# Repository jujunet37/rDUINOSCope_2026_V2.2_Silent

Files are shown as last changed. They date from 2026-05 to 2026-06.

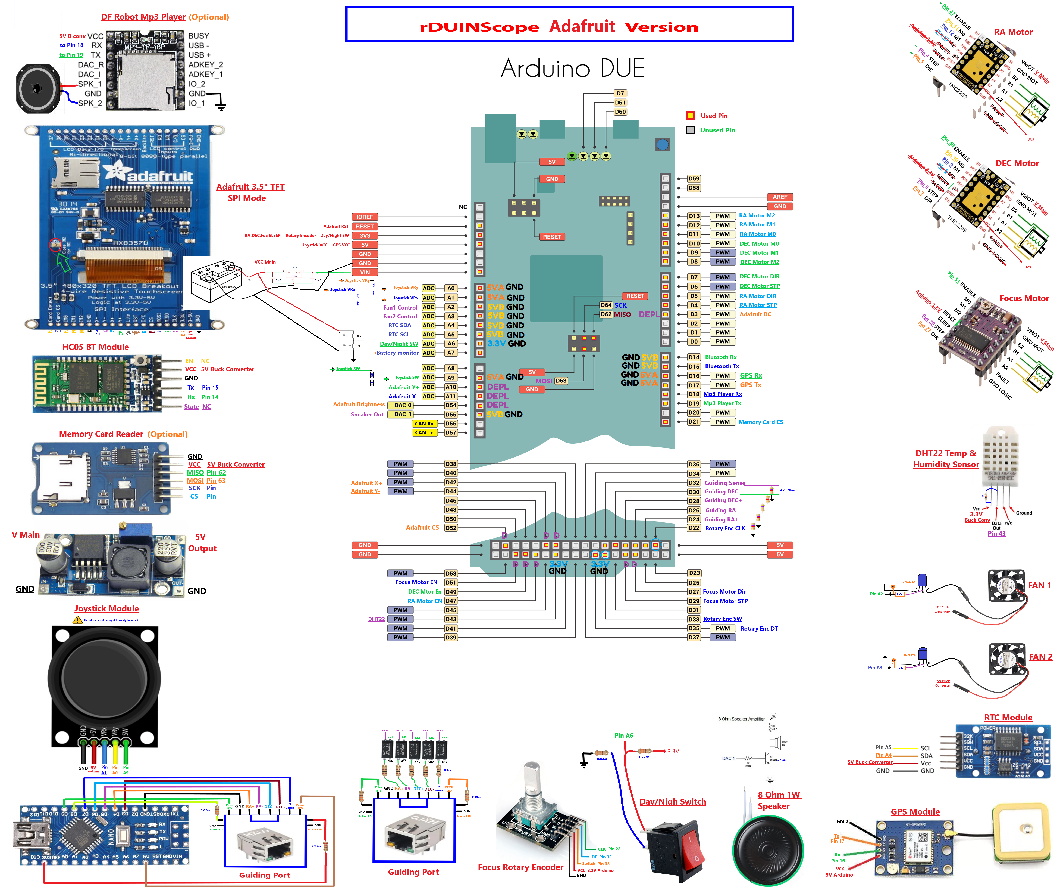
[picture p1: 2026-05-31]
Adafruit HW V.1 Wiring Diagram2.png

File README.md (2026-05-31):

# Update 24/05/2026 : rDUINOScope\_2026\_V2.2\_Silent

# 

## This is a modified version of the 10 April 2020 version of the rDUINOScope by Khairey Nouhe that works with Adafruit 3.5" 320X480 TFT SPI mode.

### New features :

* This new version need a hardware modification. It uses TMC2209 instead of DRV8825, which make the motors much more quiter.
* Joystick re-leveling, addition of very low speed manual mode.
* Modification of periodRA and DEC Timers to adjust motor speeds for these new drivers.
* Reversing motor polarity for rotation in the correct direction for these new drivers.
* Microstepping sequence moved from 1-2-4-8-16 to 8-4-16-32 for compatibility with these new drivers.
* Review of deceleration mode
* Bug fix : displayed the chain of the previous pointed-to object when loaded an object from bright star catalog : corrected.
* Speed adjusted because of lower precision on these drivers. Now 90% of "2.0 Big Update" version and 70% of "2.1 ASCOM" version, still 180% of the initial version without full step speed.

#### 

# HARDWARE REQUIREMENT :

Wire as shown in the diagram.

- Let the unused pins unplugged, and put a wire to supply the 3.3V pin from the Arduino source.
- Set the drivers to 1.5V.
To set the drivers : Measure the voltage between VREF and GND with no motors plugged, and adjust voltage with the screw.

YouTube video link : https://www.youtube.com/watch?v=LmjZzCkUyhM

---

# 

# Update 28/03/2026 : rDUINOScope\_2026\_V2.1\_ASCOM

## V2.1 major improvements : ASCOM Driver, code optimization and new search engine.

# 

### Total code revision :

* All String removed, migration to char to avoid unpredictable memory issues.
* New motor moving logic for slew, with included Arduino Due hardware timer to improve CPU performance and avoid ASCOM reading conflict.
* Speed also increase by 30% (was already doubled with previous version), so it is now 2.5x times faster to slew comparing to original version. Motors spin with less vibrations.

### New features :

* New loading menu with brand new search engine.

Be specific when searching. Engine look in the first catalog, stop when found 50 objects with the entered string. Go to the second, etc... Stop when 250 objects limit is reached. Engine don't look at planets names.

* Complete server ASCOM driver, for multiple connections with several app at the same time (Cartes du Ciel, PHD2, N.I.N.A)
* Joystick acceleration for smoothness

#### Driver support :

* GOTO object
* GOTO HOME position
* GOTO Park Position
* Set Park feature
* Set Tracking feature
* Set Rates feature
* Pier Side position
* Synchronisation
* RA/DEC reading coordinates
* ALT/AZ coordinated (calculated by the driver)
* Import GPS coordinates (LAT, LONG, ALT)
* Manual move with invert axis
* Abort move
* Autoguiding (pulse guiding) No more need an external device.

### BUG fix :

* Several stars names corrected in alignment list.
* RA/DEC coordinates : A rounding bug in coordinates made a 1m or 1' jump.
* Files on SD card may be corrupted after going into options menu (was caused by a String value)
* Meridian flip didn't occur when goto back on east and pass it a second time.
* Brightness setting woundn't work.
* BT manual move amount corrected, adaptative amount depending on DEC value
* BT slew froze the APP.
* BT slew wouldn't show telescope position during a Slew
* Display bug on OBSERVING / TRACKING line

### Known issues :

* Motors start to move when shutdown the PC with tracking ON (even with driver disconnected). Set tracking OFF before shut down the PC.

### REQUIRE :

* Arduino IDE 1.8.19

* Windows settings : Must change decimal character to "." in region settings

### Installation :

* Edit rDUIUNOScope\_FINAL and type you location on lines 191 to 193. Change worm settings (205 to 207). Flash Arduino code
* Copy files to the micro SD card (new ASCOM image files)
* Install the ASCOM driver (require ASCOM platform, tested on 7.1 Update 1

### Libraries :

* Copy to : C:\\Users\\USERNAME\\Documents\\Arduino\\libraries

* marekburiak-ILI9341\_due-13edbd2
* DHT\_sensor\_library
* TinyGPSPlus
* Touch-Screen-Library-master
* SdFat-master
* DueTimer-master
* DS3231
* Time-master
* Adafruit\_Unified\_Sensor

* Install in library manager :

* Arduino SAM Boards (32-bits ARM Cortex-M3) (v 1.6.12)

### 

### Miscellaneous :

* Setup video on YouTube.
* French : https://youtu.be/6-61nRDWkmA
* English : https://youtu.be/PrEs-5IPebA

# Update 16/07/2024 : rDUINOScope\_2024\_Big\_Update V2.0

### Corrected bugs and many new features and catalogs :

### corrected bugs :

* Previously corrected autoguiding : now works.
* Status bar : Auto and OFF superposition message for meridian flip : corrected.
* Coordinates Page : RA, DEC and HA inversion, DEC format error (missing a ":", and was in HA box : Workaround found because correct it directly make bluetooth no longer works. Now DEC in right format and BT works)
* LST and AZ/H error due to bad summer time parameters for France. Corrected for France, check the code to adjust for other countries. (same change days as for Italy (by default), but GMT + 1 for winter and GMT + 2 for summer).
* Corrected an error in dayno formula that causes a shift in RA for planets.
* Corrected an error in planets computing formulas and add precise information data.
* Corrected errors in Moon computing formulas
* RA went false or negative on Moon Goto : Corrected

### Added :

### Hardware :

* Same wiring than Khairey Nouhe design with all functionalities but focuser and fan connectors.
* Now PCB is provided, gerber files are in the package.
* Internal cooling fan, controlled by the UI.

### Software :

* Previously add dew point information.
* Previously double goto speed.
* Previously center joystick tracks and orthogonality of both axes in software (for my component, look at the previous video, 1h05m)
* Joystick directions more intuitive : left : RA return, right : RA forward.
* Add fine manual move for BlueTooth app, works great with Skysafari, works with stellarium plus but very long latency.
* Bluetooth works, tested with Skysafari 6, 7, stellarium mobile plus and Stellarium desktop.
* Add Store position utility : To memorize any position and goto back function to recall this position. Useful for keeping a frame camera when needed to go elsewhere (ex goto bright star for Bahtinov focusing and then go back to the target)
* Touchscreen calibration tool added (button was in option page but not activated). New calibration tool was created to help unshift touchzones with display. The tool can display the new correction parameters, and store it in SD card. Parameters can be fine tuned by editing "OPTION.TXT" in SD card. Four last values are : Slope in x, Slope in y, Intercept in x and intercept in y. A function can restore to default and erase SD card calibration data in case of bad calibration. Look at code comment for further informations.
* New load menu with cool JWST's creation pillars background :-)
* Checked Messier Catalog and update informations abouts objects, such as name and distance.
* Move M111 and M112, which don't exist in Messier catalog, now in NGC catalog.
* Now around 3000 objets in database !
* New NGC catalog with 2400 objects :

  * All objects in Northern hemishere down to -35° DEC, Magnitude < 13. Then filtering objects by a selection by taking into account the atmospheric extinction : ojects with Magnitude < 10 at -35° to -25° DEC, Magnitude < 11 at -25 to -20° DEC. Magnitude < 12.5 at -20 to -15° DEC. Magnitude 13 and lower for DEC > -15°.
  * NGC catalog divided in 5 parts with 480 item each. Each part with a magnitude range, for a variety of apertures.
* 186 IC catalog objetcs with same magnitude references as NGC catalog above, with no cross references with NGC.
* 172 Bright stars catalog for focusing purpose.
* 160 Double stars catalog
* 138 Variable stars catalog
* Custom catalog with up to 240 entries : completed with Collinder catalog and special objects : 84 entries.
* Deleted double references in NGC, IC catalogs and cross references with other catalogs. Priority : Messier, NGC, IC.
* All new catalogs sorted by constellation : less time to move from one to the other ! Buttons now show name, constellation and magnitude.
* Bunch of new information data (distance, separation and color for double stars, period, type and magnitudes for variable stars, etc...)
* All catalogs loaded in the same array : Same SRAM usage but now more than 3000 objects !
* New Autoguiding background : deleted circle RA, DEC, Focus. New landscape.
* Add new planet info from J2000 (1st January 2000 @ 12h GMT), previous information was approximate computed info for 2013 from J2000 data. Now starting computing from J2000 original information with better precision : On a test date, error values for internal planets was RA/DEC 4-5m/20-30'. External planets was 0-3m/2-5' (except 15-20' DEC for Mars and Neptune). Now internal planets at this test date are in range RA/DEC error : 1-2m/8-13'. External planets : 0-2m/2-7'. Tested on random dates between 2024-2044, for all planets, error are within -5m to +2m RA / -13' to 13' DEC, most values <10'.

### miscellaneous :

* Complete tutorial construction on YouTube.
* French : https://www.youtube.com/watch?v=rhm9jwSgXOs
* English : https://www.youtube.com/watch?v=H-uTFNglyio

### All changes in code are tagged by // Add JG, // End add JG, // Modif JG, for easily look at the modifications.

===========================================================

# Previous Updates From Khairey Nouhe, Giacommo Mammarella, Dessislav Gouzgounov and contributors :

### Update Friday 10/4/2020 (Fayrouz Update With ILI9341):

* The new version is built on the SdFat Library.
* It uses a modified version of marekburiak-ILI9341\_due library that has been modified specially for this project.
* New Graphical User Interface has been developed,Inspired by Dessislav Gouzgounov.
* Corrected Solar System Objects bug from last update. Thanks to (Aitor Plazaola Alcerreca) From the rDUINOScope Support Group.
* Support for Stellarium Mobile Plus has been added.
* Supports the rDUINOScope Companion Android App (will be launched soon on Google Play)!

### Hardware Changes:

* Support for PHD2 Autoguiding has been added. Thanks to the project by https://github.com/kevinferrare/arduino-st4
* A third stepper motor has been added for focus control.
* An Optional DFRobot Mp3 Player has been added for future upgrade.
* Consider the new Wiring Diagram for Hardware Changes!
===========================================================

### Update Saturday 4/5/2019 (Fayrouz Update With Solar System!):

* Removed Nextion Commands to avoid errors in compile.

### Update Tuesday 16/3/2019 (Fayrouz Update With Solar System!):

### Use IDE 1.8.5 to avoid compile errors.

Includes Giacomo Mammarellas's updated features!

* No hardware changes.
* Memory card contents are changed.
* Added Solar System objects tracking to Load Screen.
* Added Battery Power indicator to main screen, currently showing USB only, just for future upgrade.
* Added images for Solar and stellar objects to show on Main Screen. ( Memory Car items changed).
===========================================================

### Update Tuesday 3/7/2018 (Fayrouz Update!):

* Includes Giacomo Mammarellas's updated features!
* No hardware changes.
* Memory card contents are changed.
* Changed supporters logos at startup page.
* Full Hardware check and confirmation at initilize.
* More Accurate Joystick calibration at startup.
* Options' data are saved to a text file on the memory card, and will be restored and initilized during next boot.
* A new screen brightness control triangle has been added.
* New on screen messages has been added.
* Prevent (Load), (Home), (Bluetooth), and (Track) buttons to function while steppers are off. Avoiding Wrong Telescope Position coordinates while steppers are off.
* Corrected Steppers' speed during " Slew to" process . very slow>slow>fast>faster>>>>>>>>>>>fast>slow>very slow>stop>track.
* Faster browsing for Messier and treasures catalogs.
* Automatic date and time set on clockScreen() derived from GPS data: the software is able to calculate the location's time zone and to auto update from summer or winter time.
* Added an new button in Options screen to update date and time from GPS data.
* New debug mode. can be used to debug touchscreen actions.
===========================================================

### Update Saturday 23/9/2017:

### Added Giacomo Mammarellas's new features Like:

* Joypad calibration at startup. No more panic to find right values for the joypad.
* Empirial March sound function moved to confirm good initialization of the device. If no sound then you're having problems! :'(
* Automatic data and time set on clockScreen() derived from GPS data: the software is able to calculate the location's time zone and to auto update to summer or winter time.
* Custom line of text can be appended to any .csv file to display custom "Description" strings. Example: I added "rich cluster with more than 100 stars" to M11 in messier.csv
* Orange color for Name and Description when tracking objects.
* Added custom.csv wich can be used to add more custom sky objects (still to be implemented) ===========================================================

Repairs:

* Re-position Summer button at Clock Screen.
* added Green and Red colors to Screen-Timeout at the status bar.
===========================================================

## rDUINOScope

* THE WORLD'S FIRST STAND ALONE ARDUINO BASED TELESCOPE CONTROL GOTO (handheld controller).
rDUINOScope is an Open Source, Arduino Due based Telescope Control System (GOTO). Drafted as stand alone system, rDUINOScope does not need PC, Tablet or Cell Phone, nor Internet connection in order to operate and deliver stunning views! It does however supports Bluetooth and LX200 protocol to connect and be controlled by smart devices!
rDUINOScope uses database with THE BEST \~250 stellar objects ( Messier and Hidden Treasures Catalogues) and 200 stars, calculates their position on the sky and points the telescope. Implemented Alignment procedures allow for "Always in the eyepiece" experience when slewing to selected objects and once the object is in the eyepiece, the system keeps tracking it.
The best part of rDUINOScope is that it is an OPEN SOURCE SOFTWARE and HARDWARE! Few custom telescope makers have announced that they are adding or about to add it to their product line. In addition, few months ago a new HW shield board was born as a spin-off project to spare you the hassle of building your own rDUINOScope!
Published under GNU General Public License
Instructions on how to build hardware can be found on the project's website: http://rduinoscope.byethost24.com/ HACKADAY.IO Project: https://hackaday.io/project/21024-rduinoscope
Facebook: https://www.facebook.com/rDUINOScope/

### rDUINOScope v2.3.1 Boiana EQ

* Release date: 03 August 2017 Status: Stable Version Author: Dessislav Gouzgounov / Десислав Гузгнов /(deskog@gmail.com)
* v2.3.1 aims to bring all existing hardware platforms into one code base. Additionally this version introduces new features to the rDUINOScope like Screensaver, TFT brightness, MosFET to control power to DRV8825 and etc.
* Current release will also be used as a base to add the Alt/Az changes.

### New features added in v2.3.1:

* Brings all existing flavours of the hardware to use same code!
* Hardware Changes!!! - Plese reffer to the HACKADAY instructions!
* Screen Brightness control;
* Screen Auto OFF function with timeout;
* Implemented FET transistor to control power to the stepper motors;
* More BlueTooth commands added to prepare for a screenless version (or operation);
* It is now possible to control rDUINOScope without the TFT screen - so called "BLIND" version.
* BUG fixes:

  * GPS fixes;
  * SlewTo speed issues for low amperage;

### New features added in v2.3:

* Code Optimization for Performance (SlewTo now capable of speeds > 3 deg/sec);
* Added Celestial, Lunar and Solar tracking speeds;
* Added new Main Menu system for more functionality;
* Added control on 2 external devices (DEV 1 \& 2 - you can hook your Heater, Fan and etc);
* Added support for SkySafari 5 (smartphone software);
* Added build in Star Atlas showing current telescope position;
* Shows current Firmware version on Loading screen and on Bluetooth request using LX200 protocol;
* Bug fixes: o Wrong DEC movement for negative DEC values passed over Bluetooth; o LST revised in the format XX:XX;

### New features added in v2.1:

* Added “1 Star Alignment” Method;
* Added “Iterative Alignment” Method;
* Added 200 brightest stars to be used in alignment procedures;
* Added Bluetooth control from Stellarium (cloned LX200 communication protocols);
* Added Bluetooth connection with PC;
* Code has been refactored for easy reading/editing;
* Bug fixes: o Wrong DEC movement for negative DEC values; o Revised RA movement formula; o OnScreen messages have been fixed;
* Buttons move after press event was fixed;

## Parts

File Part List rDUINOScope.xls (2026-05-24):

Type | Name | Designator | Footprint | Quantity
Capacitor | Electrolytic capa 100u | C3,C4 | SMD CAP-D6.3×H5.5 | 2
Capacitor | Ceramic capa 0.33u | C1 | RAD-0.2 | 1
Capacitor | Ceramic capa 0.1u | C2,C5 | RAD-0.2 | 2
Resistor | 10K | R1 | R_AXIAL-0.3 | 1
Resistor | 20K | R2 | R_AXIAL-0.3 | 1
Resistor | 6.8K | R3 | R_AXIAL-0.3 | 1
Resistor | 330R | R4,R5 | R_AXIAL-0.3 | 2
Resistor | 47k | R6,R8,R10 | R_AXIAL-0.3 | 3
Resistor | 100k | R7,R9,R11 | R_AXIAL-0.3 | 3
Resistor | 220R | R12 | R_AXIAL-0.3 | 1
Resistor | 6.8R | R13 | R_AXIAL-0.3 | 1
Resistor | 330 | R14 | R_AXIAL-0.3 | 1
Resistor | 10k | R15 | R_AXIAL-0.3 | 1
Resistor | 100R | R16,R17,R18,R19,R20 | R_AXIAL-0.3 | 5
Resistor | 4.7k | R21,R22,R23,R24,R25 | R_AXIAL-0.3 | 5
Transistor | 2N3904(TO-92) | Q1 | TO-92-3_L5.1-W4.1-P1.27-L | 1
Transistor | 2N2222 | Q2 | TO-92-3_L4.9-W3.7-P1.27-L | 1
Transistor | 7809 MOSFET | 7809 | TO-220-3_L10.0-W4.5-P2.54-L | 1
Optocoupler | PC817 optocoupler | U5,U6,U7,U8,U4 | DIP-4_L4.6-W6.5-P2.54-LS7.6-BL | 5
Driver | DRV8825 | U2, U3 | DRV8825 | 2
Connector | RJ45 connector | RA and DEC | RJ45-TH_R-RJ45R10P-B000 | 2
Connector | RJ12 connector | AG | RJ11-TH_PCB-6P6C-90 | 1
Connector | Ribbon screen connector | SCREEN | CONN-TH_HC-ZH1.5-8A | 2
Connector | Header JST 1.25 x 2 | Fan, Speaker, switch | 1X02-1.25MM_JST | 3
Connector | Header JST 1.25 x 3 | DHT22 | 1X03-1.25MM_JST | 1
Connector | Header JST 1.25 x 4 | GPS Module | 1X04-1.25MM_JST | 1
Connector | Header JST 1.25 x 5 | Joystick, bridge x 2 | 1X05-1.25MM_JST | 3
Connector | Header JST XH 2.54 | POWERIN | HDR-TH_2P-P2.54-V-M | 1
Fan | 20x20x6mm 2 pin 5V |  | ACP2006 | 1
Type : | Name : | Reference |  | Quantity
Screen | TFT Adafruit 3,5" | 2050 (HX8357D) |  | 1
Board | Arduino Due |  |  | 1
Board | Arduino Nano | ATMega 328P |  | 1
BT module | BT | HC05 BT |  | 1
5V Buck | Based on LM2596 |  |  | 1
Joystick |  |  |  | 1
Switch | 8x8x8.4mm | ON/OFF lock L068-A |  | 1
Speaker | Speaker | 8 Ohm 1W |  | 1
GPS Module |  | GY-NEO6MV2 |  | 1
RTC module |  | DS3231 |  | 1
T°/H% sensor |  | DHT22 4 pins |  | 1
Drivers | Polulu, TI chip 8825 | DRV8825 |  | 3
Motors | Nema 17 | JK42HM40-1684 |  | 2
Holders | In GitHub package | https://www.thingiverse.com/thing:4853748
 |  | (add 2 bases and cover on thing:4682671)
 |  | replace 2 motors holders and connector squares
RJ45 cables | 1,5m lenght |  |  | 1
RJ45 cables | 1m lenght |  |  | 1
Pulleys | motor pulleys | GT2/6mm 16t trou 5mm |  | 2
Pulleys | Worm pulleys | GT2/6mm 48t trou 6mm |  | 2
Belt | belt | 6mm GT2-148 |  | 2
RJ12 cable | for Autoguiding | 50cm |  | 1
Screws
TCHC M6X20 (Hollow hexagonal head) |  |  |  | 1
TCHC M6X35 |  |  |  | 1
TBHC M3X8 (Cambered head hexagonal hollow) |  |  |  | 12
TBHC M3X20 |  |  |  | 4
nut M6 |  |  |  | 2
nut M3 |  |  |  | 8
nut M4 |  |  |  | 2
TBHC M4x25 |  |  |  | 2
washer M03 |  |  |  | 8
Autoguiding box | Plastic | 61x36x25mm |  | 1

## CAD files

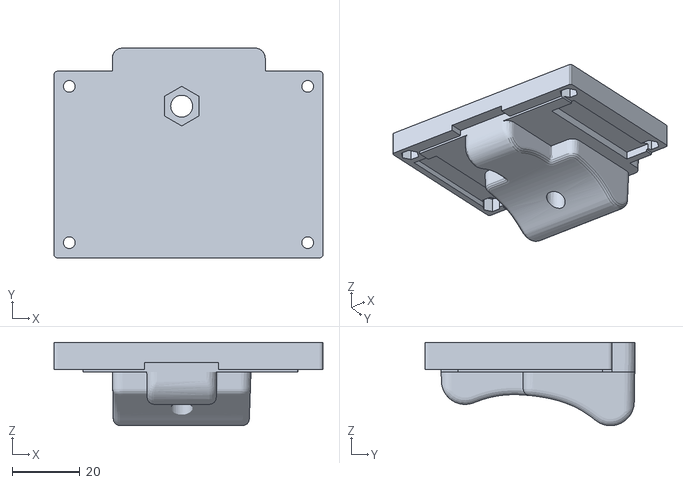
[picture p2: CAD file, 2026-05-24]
NEQ5_Holders_STL_FILES (oddvarness Thingiverse)/RA_base.stl
79.2 x 61.8 x 24.5

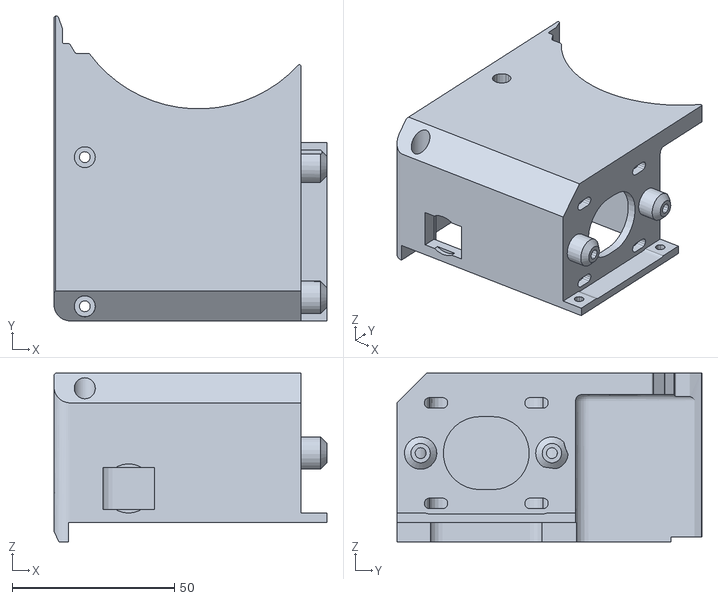
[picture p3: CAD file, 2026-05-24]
NEQ5_Holders_STL_FILES (oddvarness Thingiverse)/RA_motor_holder_V2_RJ45.STL
84.2 x 94.0 x 52.1

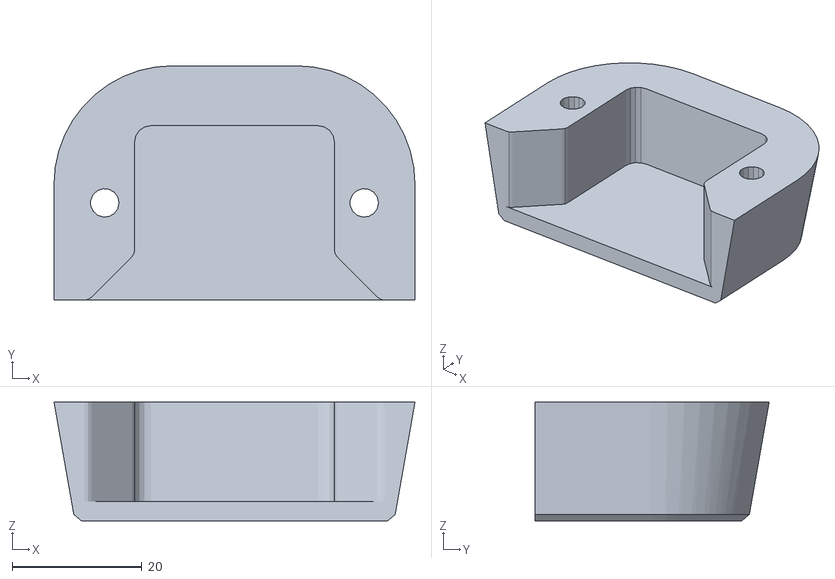
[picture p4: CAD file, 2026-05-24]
NEQ5_Holders_STL_FILES (oddvarness Thingiverse)/DEC_brace.stl
55.7 x 36.1 x 18.3

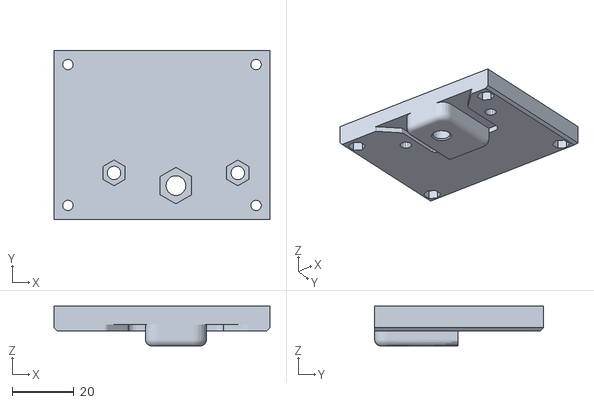
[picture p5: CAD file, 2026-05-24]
NEQ5_Holders_STL_FILES (oddvarness Thingiverse)/DEC_plate_V2.stl
69.8 x 54.5 x 12.9

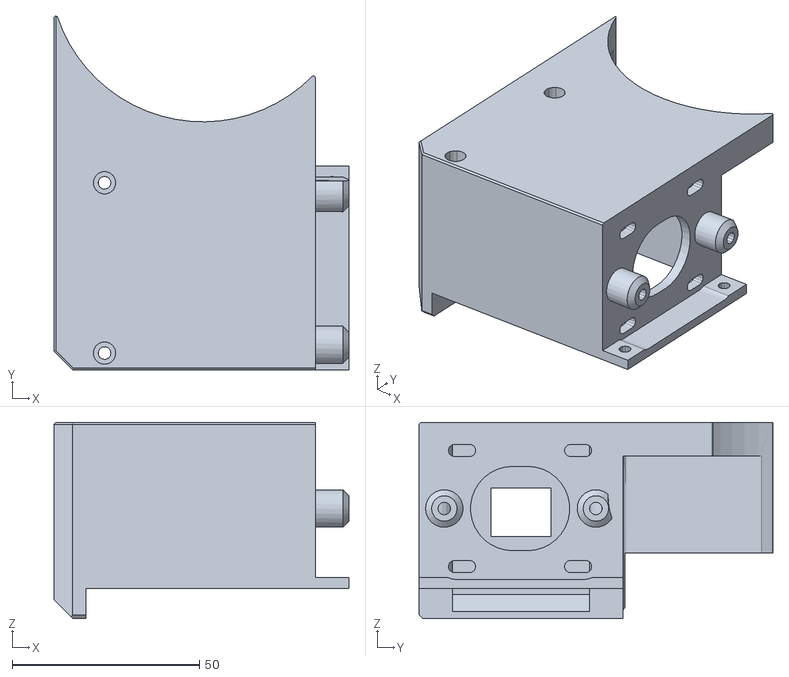
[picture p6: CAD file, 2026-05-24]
NEQ5_Holders_STL_FILES (oddvarness Thingiverse)/DEC_motor_holder_V2_RJ45.STL
78.8 x 94.5 x 52.4

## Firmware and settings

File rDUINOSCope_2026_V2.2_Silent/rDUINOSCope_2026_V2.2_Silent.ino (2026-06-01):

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
//    PROJECT Website: http://rduinoscope.tk/"motors spin in the wrong way"
//
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
//    ALLIGNMENT Method: 1 Star Alignment - The method I have implemented is part of Mr. Ralph Pass alignment procedure described on http://rppass.com/
//                       Mr. Pass helped rDUINOScope by providing the calculations needed to implement the method. http://rppass.com/align.pdf - the actual PDF
//
//                       Iterative Alignment - The method is based on article from "New" Hamilton Astronomy.com website: http://astro.hcadvantage.com
//                       Actual PDF document: http://astro.hcadvantage.com/ASTRO_ARTICLES/Polar_Alignment_Part_II.pdf
// Note: the Adafruit version has been built upon a modified version of the ILI9341_due by https://github.com/marekburiak.
// Coding and GUI Designs have been developed by Khairey Nouhe as a contribution to the rDUINOScope Support community!
//
////////////////////////////////////////////////
#include <ILI9341_due_config.h>
#include <ILI9341_due.h>
#include "gfxfont.h"
#include "DHT.h"
#include <TinyGPS++.h>
#include <Time.h>
#include "TouchScreen.h"
#include <SdFat.h>
#include <DueTimer.h>
#include <DS3231.h>
#include <math.h>
#include <TimeLib.h>
#include "defines.h"
//#include "DFRobotDFPlayerMini.h"
#include <string.h>

char textBuff[20];
//#define serial_debug       // comment out to deactivate the serial debug mode
#define use_battery_level // comment out to deactivate battery level option

//// New search engine screen feature
#define SCREEN_LOAD_MENU 17
#define SCREEN_SEARCH_OBJECT 16
// Button types
#define BUTTON_PRIMARY 0
#define BUTTON_SECONDARY 1
#define BUTTON_GO 2
#define BUTTON_CANCEL 3
// Colors
#define LIGHTBLUE 0x7D7C
#define LIGHTGRAY 0xC618
#define DARKGRAY 0x7BEF
#define BLUE 0x001F
#define RED 0xF800
#define GREEN 0x07E0
#define YELLOW 0xFFE0
#define WHITE 0xFFFF
#define BLACK 0x0000
// Search vars
char searchQuery[50] = "";
char searchResults[50][50]; // Stores the names of the results
char searchCatalog[50][20]; // Stores the catalog of each result
float searchRA[50];
float searchDEC[50];
int searchResultCount = 0;
int selectedResult = -1;
int currentSearchPage = 0;
// keyboard
int keyboardCursor = 0;
bool keyboardVisible = true; // always visible
// Definitions of the enlarged keyboard
char keyboardLayout[4][10] = {
    {'1','2','3','4','5','6','7','8','9','0'},
    {'Q','W','E','R','T','Y','U','I','O','P'},
    {'A','S','D','F','G','H','J','K','L','_'},
    {'Z','X','C','V','B','N','M','<',' ',' '}
};
// scrollbar vars
int scrollOffset = 0;
int totalResults = 0;


//// ASCOM variables added

// Global vars
volatile bool ascomConnected = false;
unsigned long lastSend = 0;
unsigned long lastASCOMMove = 0;
const unsigned long ASCOM_PROTECTION_TIME = 500; // 500ms protection after ASCOM movement
volatile bool isAtHome = false;
volatile bool isAtPark = false;
volatile bool isParkOperation = false;
volatile bool isHomeOperation = false;
bool MERFLIPRESET = false;
unsigned long Slew_Timer_flag = 0;

// === SERIAL COMM VARS ===
#define SERIAL_OUTPUT_BUFFER_SIZE 512
#define SERIAL_INPUT_BUFFER_SIZE 100
// Serial Buffers
char serialOutputBuffer[SERIAL_OUTPUT_BUFFER_SIZE];
volatile uint16_t outputHead = 0;
volatile uint16_t outputTail = 0;
volatile bool serialTxActive = false;
char serialInputBuffer[SERIAL_INPUT_BUFFER_SIZE];
volatile uint8_t inputIndex = 0;
// command flags 
volatile bool slewCommandReceived = false;
volatile bool moveCommandReceived = false;
volatile bool parkCommandReceived = false;
volatile bool homeCommandReceived = false;
volatile bool trackingCommandReceived = false;
volatile bool stopCommandReceived = false;
// Buffers waiting commands
char pendingSlewCommand[100];
char pendingMoveCommand[100];
char pendingParkCommand[100];
char pendingTrackingCommand[100];
bool IS_CRITICAL_MOVEMENT = false;
bool locationSent = false;
bool guideCommandReceived = false;
char pendingGuideCommand[50];
unsigned long guideStartTime = 0;
int guideDuration = 0;
bool isGuiding = false;
char currentGuideDirection[20] = "";
unsigned long lastGuidePulse = 0;
const int GUIDE_PULSE_INTERVAL = 2;
bool trackingPending = false;
bool slewascomsent = false;
bool syncCommandReceived = false;
char pendingSyncCommand[128] = {0};

volatile bool moveActive = false;
enum MoveAxis_e { MOVE_AXIS_NONE = 0, MOVE_AXIS_RA, MOVE_AXIS_DEC };
volatile MoveAxis_e moveAxis = MOVE_AXIS_NONE;
volatile bool moveDirPositive = true;
volatile int moveMicroStepMode = 16;
volatile float moveRate = 0.0;
unsigned long move_lastMicros = 0;
uint8_t move_pulseState = 0; // 0 = idle / ready to set HIGH, 1 = HIGH, waiting to set LOW
const unsigned long move_pulseHighMicros = 1000UL;
const unsigned long move_pulseLowMicros  = 1000UL;

bool DEC_accelerationDone = false;
bool RA_accelerationDone = false;
int DEC_accel_step = 0;
int RA_accel_step = 0;

bool trackingWasActiveBeforeMove = false;

//End ASCOM variables

// === GLOBAL VARS FOR HARDWARE TIMERS ===
volatile bool slewRA_active = false;
volatile bool slewDEC_active = false;
volatile long slewRA_targetSteps = 0;
volatile long slewDEC_targetSteps = 0;
volatile int slewRA_currentDir = LOW;
volatile int slewDEC_currentDir = LOW;

// Flag to check if the slew has been initialized
bool slewInitialized = false;
static unsigned long lastDecelCheck = 0;
//----------------

#define RA_START_DELAY_MS 5000  // Start RA delay (milliseconds)
// Decel thesholds
#define DECEL_THRESHOLD_MODE_8  120000  // Stay @ 8 until // modified for 2209
#define DECEL_THRESHOLD_MODE_16  60000   // Go from 8 to 16
#define DECEL_THRESHOLD_MODE_32  40000   // Go from 16 to 32
#define DECEL_THRESHOLD_MODE_64  20000   // Go from 32 to 64
unsigned long RA_startRequestTime = 0;  // Moment where RA start
bool RA_waitingToStart = false;
//----------------

// Firmware & Hardware Versions
const char FirmwareDate[] PROGMEM = "9/4/2020";
const char FirmwareNumber[] PROGMEM = "v2.3.1 Boiana-Adafruit";
const char FirmwareName[] PROGMEM = "rDUINOScope Boiana-EQ V2.3.1";
const char FirmwareTime[] PROGMEM = "12:00:00";

// Default values to load when CANCEL button is hit on the GPS screen ( Change by your Home Location!)

float OBSERVATION_LATTITUDE = 47.0000; // (Type your location
float OBSERVATION_LONGITUDE = 0.0000; // (Type your location)
float OBSERVATION_ALTITUDE = 100; // (Type your location)
int TIME_ZONE = 1;                   // France
// .............................................................
unsigned long startTime;
unsigned int  duration;
// HERE GOES THE Mount, Gears and Drive information.
// ... used to calculate the HourAngle to microSteps ratio
// UPDATE THIS PART according to your SET-UP
// ---------------------------------------------
// NB: RA and DEC uses the same gear ratio (144 tooth in my case)!
//----------------------------------------------

int WORM = 144; // For NEQ5 (144 teeth on both axies)
int REDUCTOR = 3;      // 1:3 gear reduction 16 and 48 teeth pulleys
int DRIVE_STP = 400;   // Stepper drive have 400 steps per revolution
int MICROSteps = 64;   // I'll use 1/16 microsteps mode to drive sidereal - also determines the LOWEST speed. // TMC2209 uses 64/32/16/8 microsteps

// below variables are used to calculate the paramters where the drive works
#define ARCSEC_F_ROTAT 1296000   // ArcSeconds in a Full earth rotation;
#define SIDEREAL_DAY 86164.0905   // Sidereal day in seconds
float ArcSECstep;
int MicroSteps_360;
int RA_90;  // How much in microSteps the RA motor have to turn in order to make 6h = 90 degrees;
int DEC_90;   // How mich in microSteps the DEC motor have to turn in order to make 6h = 90 degrees;
int HA_H_CONST;
int HA_M_CONST;
int DEC_D_CONST;
int DEC_M_CONST;
int MIN_TO_MERIDIAN_FLIP = 2;   // This constant tells the system when to do the Meridian Flip. "= 2" means 2 minutes before 24:00h (e.g. 23:58h)
int MIN_SOUND_BEFORE_FLIP = 3;   // This constant tells the system to start Sound before it makes Meridian Flip
float mer_flp;                   // The calculateLST_HA() function depending on this timer will convert the HA and DEC to the propper ones to do the flip.
boolean MERIDIAN_FLIP_DO = false;
int Tracking_type = 1;  // 1: Sidereal, 2: Solar, 0: Lunar;
int Clock_Sidereal;  // Variable for the Interruptions. nterruption is initialized depending on the DATA above -in miliseconds
int Clock_Solar;  // Variable for the Interruptions. nterruption is initialized depending on the DATA above -in miliseconds
int Clock_Lunar;  // Variable for the Interruptions. nterruption is initialized depending on the DATA above -in miliseconds

// NEW BRIGHTNESS CONTROL
volatile int pwm_duty = 255; // 0-255
volatile int pwm_counter = 0;

///////////////////////////////////////////////////// Modules Setup /////////////////////////////////////////////////////

///////////////////////////////////////////////////// Adafruit 3.5" & ILI9488 TFT Setup /////////////////////////////////////////////////////
// The display uses hardware SPI
/** ILI9488 pin map */
#define TFT_CS  52
#define TFT_DC  3
#define TFT_RST -1
#define TFTBright DAC0
//ILI9488 tft(TFT_CS, TFT_DC, TFT_RST);
ILI9341_due tft = ILI9341_due(TFT_CS, TFT_DC, TFT_RST);  //ILI9340
#define SD_CS 21    // Chip Select for SD card
#define SD_SPI_SPEED SPI_HALF_SPEED  // SD card SPI speed,SPI_HALF_SPEED, try SPI_FULL_SPEED >> doesn't work
SdFat SD; // set filesystem

// These are the four touchscreen analog pins
#define YP A10  // Y+ to A10   >>> must be an analog pin
#define XM A11  // X- to A11   >>> must be an analog pin
#define YM 44   // Y- to 44    >>> a digital pin
#define XP 42   // X+ to 42    >>> a digital pin

// This is calibration data for the raw touch data to the screen coordinates
#define TS_MINX 120  // touch Left margin  >>> Default value is 110 
#define TS_MINY 90   // touch up margin    >>> Default value is 80
#define TS_MAXX 850  // touch Right margin >>> Default value is 900  
#define TS_MAXY 930  // touch Down margin  >>> Default value is 940 

#define MINPRESSURE 5    // Minimum Pressure Touch Sensitivity >>> Default value is 10
#define MAXPRESSURE 1000 // Maximum Pressure Touch Sensitivity >>> Default value is 1000
TouchScreen ts = TouchScreen(XP, YP, XM, YM, 300);

///////////////////////////////////////////////////// Other Modules Setup /////////////////////////////////////////////////////

#define DHTPIN 43
#define DHTTYPE DHT22
DS3231 rtc(A4, A5);           // (SDA-A4, SCL-A5) from the RTC board
DHT dht(DHTPIN, DHTTYPE);
TinyGPSPlus gps;             // (Rx-16, Tx-17)

/** NIGHT MODE ANALOG pin */
#define DAY_NIGHT_PIN A6

//Joystick Pins//
int yPin = A0;
int xPin = A1;
int Joy_SW = A9;
int x_cal, y_cal = 0;

int FAN1 = 25;
int speakerOut = DAC1;         // Was 2
int BAT_PIN = A7;             //Analog channel A7 as used to measure BAT_PIN voltage

// Stepper Motors Setup
int RA_EN = 47;
int RA_STP = 4;
int RA_DIR = 5;
int RA_MODE0 = 11; // PD7
int RA_MODE1 = 12; // PD8
int RA_MODE2 = 13; // PB27

int DEC_EN = 49;
int DEC_STP = 6;
int DEC_DIR = 7;
int DEC_MODE0 = 10; // PC29
int DEC_MODE1 = 9; // PC21
int DEC_MODE2 = 8; // PC22

////////////////////////Auto Guiding Setup ////////////////////////////////////
int RA_PlusPin = 24;
int RA_MinusPin = 26;
int DEC_PlusPin = 28;
int DEC_MinusPin = 30;
int Guiding_Sense = 32;
bool IS_CONNECTED = false;
boolean IS_PulseGuiding = false;
#define CH0_OFFSET  (46 - LEVEL_HIGH/2)
#define CH1_OFFSET  (CH0_OFFSET + 62 * 1)
#define CH2_OFFSET  (CH0_OFFSET + 62 * 2)
#define CH3_OFFSET  (CH0_OFFSET + 62 * 3)
#define LEVEL_HIGH      (30)
#define LEVEL_LOW       (0)
static uint8_t ch0_data = LEVEL_LOW;
static uint8_t ch1_data = LEVEL_LOW;
static uint8_t ch2_data = LEVEL_LOW;
static uint8_t ch3_data = LEVEL_LOW;
////////////////////////////////////////////////////////////////////////////////////
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
void loop(void) {

//Add JG ASCOM
// Serial communication (USB/ASCOM)

runMoveTask();

if ((trackingWasActiveBeforeMove) && (millis()-lastASCOMMove)>200 && IS_OBJ_FOUND) {
        IS_TRACKING = true;
        startTracking();
        sendTrackingStatus();
        trackingWasActiveBeforeMove=0;
}

    if (slewCommandReceived) {
        handleSlewCommand(pendingSlewCommand);
        slewCommandReceived = false;
    }
    
    if (moveCommandReceived) {
        handleMoveCommand(pendingMoveCommand);
        moveCommandReceived = false;
    }
    
    if (parkCommandReceived) {
        handleParkCommand(pendingParkCommand);
        parkCommandReceived = false;
    }
    
    if (homeCommandReceived) {
        handleHomeCommand();
        homeCommandReceived = false;
    }
    
    if (trackingCommandReceived) {
        handleTrackingCommand(pendingTrackingCommand);
        trackingCommandReceived = false;
    }
    
    if (stopCommandReceived) {
        handleStopCommand();
        stopCommandReceived = false;
    }

    if (syncCommandReceived) {
    handleSyncCommand(pendingSyncCommand);
    syncCommandReceived = false;
    pendingSyncCommand[0] = '\0';
    }

    if (guideCommandReceived) {
        handleGuideCommand(pendingGuideCommand);
        guideCommandReceived = false;
    }
    processSerialBuffer();
    processGuiding();
    
    // === PERIODIC COORDINATE SEND ===
    if (millis() - lastSend > 2000) {
        Current_RA_DEC();
        sendTelescopeCoordinates();
        lastSend = millis();
    }

if (IS_CRITICAL_MOVEMENT && (millis() - lastASCOMMove) > ASCOM_PROTECTION_TIME) {
    IS_CRITICAL_MOVEMENT = false;
}
// End add ASCOM

  // AutoGuiding control .... if Any!
  if (CURRENT_SCREEN == 14 && digitalRead (Guiding_Sense) == HIGH)
  {
    if (IS_CONNECTED == false)
    {
      OnScreenMsg(8);
      if (IS_SOUND_ON) {
        SoundOn(note_C, 32);
        delay(200);
        SoundOn(note_C, 32);
        delay(200);
        SoundOn(note_C, 32);
        delay(1000);
      }
      drawAutoGuidingScreen();
      IS_CONNECTED = true;
    }

    IS_PulseGuiding = true;
    CURRENT_SCREEN = 14;
    considerPulseGuiding();
  }
  else if (CURRENT_SCREEN == 4 && digitalRead (Guiding_Sense) == HIGH)
  {
    if (IS_CONNECTED == true)
    {
      OnScreenMsg(8);
      if (IS_SOUND_ON) {
        SoundOn(note_C, 32);
        delay(200);
        SoundOn(note_C, 32);
        delay(200);
        SoundOn(note_C, 32);
        delay(1000);
      }
      IS_CONNECTED = false;
    }
    CURRENT_SCREEN = 14;
    drawAutoGuidingScreen();
    IS_PulseGuiding = true;
    considerPulseGuiding();
  } else if (CURRENT_SCREEN == 14 && digitalRead (Guiding_Sense) == LOW && IS_CONNECTED == true && IS_PulseGuiding == true )
  {
    OnScreenMsg(9);
    if (IS_SOUND_ON) {
      SoundOn(note_C, 32);
      delay(200);
      SoundOn(note_C, 32);
      delay(200);
      SoundOn(note_C, 32);
      delay(1000);
    }
    CURRENT_SCREEN = 14;
    drawAutoGuidingScreen();
    IS_PulseGuiding = false;
    IS_CONNECTED = false;
  }

  // This is done in order to prevent multiple calculations of LST_HA per second (especially while SlewTo) and only
  // do it once the DEC SlewTo slows down, but before stopping OR once every 10 seconds (in order to do the Meridian Flip)

  if (RA_move_ending == 1 && (millis() - lastASCOMMove) > ASCOM_PROTECTION_TIME) {  //Modif ASCOM
  calculateLST_HA();
}

  if ((IS_MERIDIAN_FLIP_AUTOMATIC) && ((UPD_LST + 10000) <= millis()) && (IS_OBJ_FOUND == true) && (millis() - lastASCOMMove) > ASCOM_PROTECTION_TIME) {  //Modif ASCOM
  calculateLST_HA();
  UPD_LST = millis();
}

  // Adding this delay to SLOW DOWN the Arduino so that the motors can catch up!
  // The delay is only needed when in full speed.... otherways the CalculateLST_HA() takes over and
  // slows down the arduino enough. CalculateLST_HA() when slewing only fires when the motors slows down
  // after they are very close to the Object Position.

if ((DELAY_Slew + 10 <= millis()) && (IS_OBJ_FOUND == false)) {   /// 1 dans l'original à la place de 10
  if (IS_STEPPERS_ON) {
    cosiderSlewTo_NonBlocking();
  } else {
    IS_OBJECT_RA_FOUND = true;
    IS_OBJECT_DEC_FOUND = true;
    IS_OBJ_FOUND = true;
    RA_move_ending = 0;
    slewInitialized = false;  // <-- AJOUTER
    stopSlewRA();
    stopSlewDEC();
  }
  DELAY_Slew = millis();
}

if (IS_OBJ_FOUND == true || (IS_OBJ_FOUND == false && Serial3.available() > 0)) 
  
  {
    // BLUETOOTH Considerations ? ... if any
    if ((IS_BT_MODE_ON == true) && (Serial3.available() > 0) && (IS_MANUAL_MOVE == false))
    {
      //BT_COMMAND_STR = Serial3.readStringUntil('#');
      char buffer[256]; // Buffer temporaire
      int bytesRead = Serial3.readBytesUntil('#', buffer, sizeof(buffer) - 1);
      buffer[bytesRead] = '\0'; // Null-terminator
      safeStringCopy(BT_COMMAND_STR, buffer, sizeof(BT_COMMAND_STR));

#ifdef serial_debug
      Serial.println(BT_COMMAND_STR);
#endif
      considerBTCommands();
      drawBin("objects/BT.bin", 0, 143, 320, 135);
    }

    // JOYSTICK Movements ? ... if any
    xPosition = analogRead(xPin);
    yPosition = analogRead(yPin);

    if ((xPosition < x_cal - 100) || (xPosition > x_cal + 100) || (yPosition < y_cal - 100) || (yPosition > x_cal + 100)) // all were 100
    {
#ifdef serial_debug
      Serial.print("xPin = ");
      Serial.println(xPosition);
      Serial.print("yPin = ");
      Serial.println(yPosition);
#endif
      IS_MANUAL_MOVE = true;
      if (IS_STEPPERS_ON)
      {
        consider_Manual_Move(xPosition, yPosition);
      }
    }
    else
    {
      IS_MANUAL_MOVE = false;
    }

    // This will take care of turning OFF the TFT's background light if the device is not used
    // for XXX amont of seconds and IS_IN_OPERATION = TRUE

    if ((TFT_timeout > 0) && (millis() - TFT_Timer > TFT_timeout) && (IS_TFT_ON) && (IS_IN_OPERATION))
    {
      setDisplayBrightness(0);
      IS_TFT_ON = false;
    }

    // TOUCH SCREEN Inputs ? ... if any

    TSPoint p = ts.getPoint();

    // Scale from ~0->1000 to tft.width using the calibration #'s

    p.x = map(p.x, TS_MINX, TS_MAXX, 0, tft.width());
    p.y = map(p.y, TS_MINY, TS_MAXY, 0, tft.height());

    int tx, ty;

    tx = (p.x - 0);
    ty = (p.y - 0);

    // we have some minimum pressure we consider 'valid'
    // pressure of 0 means no pressing!

    if (p.z < MINPRESSURE || p.z > MAXPRESSURE) {
      return;
    }
    /*
           //Useful to debug touch:
         #ifdef serial_debug
           Serial.print(" -> Touched: ");
           Serial.print(tx);
           Serial.print(", y = ");
           Serial.println(ty);
         #endif
    */
    considerTouchInput(tx, ty);

    // OTHER UPDATES ?  ... if any
    // Happens every 2 seconds
    if (((millis() - UPD_T) > 2000) && (IS_MANUAL_MOVE == false) && (millis() - lastASCOMMove) > ASCOM_PROTECTION_TIME) {

      calculateLST_HA();  // Make sure it Updates the LST! used on Main Screen and When Calculating current Coords.
      considerTimeUpdates();
      considerDayNightMode();
      considerTempUpdates();

      // Add MF correction
      if (((millis() - Slew_timer) > 120000) && (MERFLIPRESET = true)) {
      MERFLIPRESET = false;
      MERIDIAN_FLIP_DO = false;
      }

      
      // I need to make sure the Drives are not moved to track the stars,
      // if Object is below horizon ALT < 0 - Stop tracking.
      if ((ALT <= 0) && (IS_TRACKING == true) && (IS_IN_OPERATION == true))
      {
        IS_TRACKING = false;
        Timer3.stop();
        drawMainScreen();
        sendTrackingStatus();
      }
      UPD_T = millis();
    }
  }
}

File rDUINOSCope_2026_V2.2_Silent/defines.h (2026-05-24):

#define BLACK           0x0000      /*   0,   0,   0 */
#define NAVY            0x000F      /*   0,   0, 128 */
#define DarkGreen       0x03E0      /*   0, 128,   0 */
#define DarkCyan        0x03EF      /*   0, 128, 128 */
#define Maroon          0x7800      /* 128,   0,   0 */
#define Purple          0x780F      /* 128,   0, 128 */
#define Olive           0x7BE0      /* 128, 128,   0 */
#define LightGrey       0xC618      /* 192, 192, 192 */
#define DarkGrey        0x7BEF      /* 128, 128, 128 */
#define Blue            0x001F      /*   0,   0, 255 */
#define GREEN           0x07E0      /*   0, 255,   0 */
#define Cyan            0x07FF      /*   0, 255, 255 */
#define RED             0xF800      /* 255,   0,   0 */
#define Magenta         0xF81F      /* 255,   0, 255 */
#define YELLOW          0xFFE0      /* 255, 255,   0 */
#define WHITE           0xFFFF      /* 255, 255, 255 */
#define orange          0xFD20      /* 255, 165,   0 */
#define GreenYellow     0xAFE5      /* 173, 255,  47 */
#define Pink            0xF81F

#define  note_c     3830    // 261 Hz
#define  note_cb    3610    // 261 Hz
#define  note_d     3400    // 294 Hz
#define  note_e     3038    // 329 Hz
#define  note_f     2864    // 349 Hz
#define  note_g     2550    // 392 Hz
#define  note_gb    2411    // 392 Hz
#define  note_a     2272    // 440 Hz
#define  note_b     2028    // 493 Hz
#define  note_C     1912    // 523 Hz
#define  note_X     1650    //

const char* ss_planet_names[] = {"SUN", "MERCURY", "VENUS", "EARTH", "MARS", "JUPITER", "SATURN", "URANUS", "NEPTUNE", "PLUTO", "MOON"};

//Updated with high precision J2000 mean orbital elements

double i[10] = {0.0, 7.00497902, 3.39467605, -0.00001531, 1.84969142, 1.30439695, 2.48599187, 0.77263783, 1.77004347, 17.14175}; // i Inclination
double o[10] = {0.0, 48.33076593, 76.67984255, 0.0, 49.55953891, 100.47390909, 113.66242448, 74.01692503, 131.78422574, 110.30347}; // o Longitude of the Ascending Node
double pl[10] = {0.0, 77.45779628, 131.60246718, 102.93768193, -23.94362959, 14.72847983, 92.59887831, 170.95427630, 44.96476227, 224.06676}; // pl Longitude of Perihelion
double a[10] = {0.0, 0.38709927, 0.72333566, 1.00000261, 1.52371034, 5.20288700, 9.53667594, 19.18916464, 30.06992276, 39.48168677}; // a Mean distance : distance from the Sun in UA
double n[10] = {0.0, 4.09233676, 1.6021293367, 0.985611, 0.523998, 0.083099, 0.033460358, 0.011731352, 0.006002, 0.003974}; // n Daily motion : number of degrees traveled in the orbit during an Earth day
double e[10] = {0.0, 0.20563593, 0.00677672, 0.01671123, 0.09339410, 0.04838624, 0.05386179, 0.04725744, 0.00859048, 0.24880766}; // e Eccentricity
double L[10] = {0.0, 252.25032350, 181.97909950, 100.46457166, -4.55343205, 34.39644051, 49.95424423, 313.23810451, -55.12002969, 238.92881}; // L Mean Longitude (orbital position for each planet on the date of the recorded elements)
double M[10], v[10], r[10], x[10], y[10], z[10], X[10], Y[10], Z[10], Xq[10], Yq[10], Zq[10], ra[10], dec_x[10];

//double i[10] = {0.0, 7.0052, 3.3949, 0.0, 1.8496, 1.3033, 2.4869, 0.7728, 1.7692, 17.1695}; //original informations
//double o[10] = {0.0, 48.493, 76.804, 0.0, 49.668, 100.629, 113.732, 73.989, 131.946, 110.469};
//double pl[10] = {0.0, 77.669, 131.99, 103.147, 336.322, 14.556, 91.500,  169.602, 6.152, 223.486};
//double a[10] = {0.0, 0.387098, 0.723327, 1.0000, 1.523762, 5.20245, 9.52450, 19.1882, 29.9987, 39.2766};
//double n[10] = {0.0, 4.09235, 1.60215, 0.985611, 0.523998, 0.083099, 0.033551, 0.011733, 0.006002, 0.004006};
//double e[10] = {0.0, 0.205645 , 0.006769, 0.016679, 0.093346, 0.048892, 0.055724, 0.047874, 0.009816, 0.246211};
//double L[10] = {0.0, 93.8725, 233.5729, 324.5489, 82.9625, 87.9728, 216.6279, 11.9756, 335.0233, 258.8717};
//double M[10], v[10], r[10], x[10], y[10], z[10], X[10], Y[10], Z[10], Xq[10], Yq[10], Zq[10], ra[10], dec_x[10];
double d, dfrac, dno;
int dd, mm, yy, hh, mu;
const double rads = (M_PI / 180.0);
const double degs = 180.0 / (M_PI);

//Don't alter or you're screwed!!
const volatile double tab[13][6] =
{
  {0, 0,  1, 0, 6288774, -20905355}, // moon data, checked by JG
  {2, 0, -1, 0, 1274027,  -3699111},
  {2, 0,  0, 0,  658314,  -2955968},
  {0, 0,  2, 0,  213618,   -569925},
  {0, 1,  0, 0, -185116,     48888},
  {0, 0,  0, 2, -114332,     -3149},
  {2, 0, -2, 0,  58793,     246158},
  {2, -1, -1, 0,  57066,    -152138},
  {2, 0,  1, 0,  53322,    -170733},
  {2, -1, 0, 0,  45758,    -204586},
  {0, 1, -1, 0, -40923,    -129620},
  {1, 0,  0, 0, -34720,     108743},
  {0, 1,  1, 0, -30383,     104755}
};
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

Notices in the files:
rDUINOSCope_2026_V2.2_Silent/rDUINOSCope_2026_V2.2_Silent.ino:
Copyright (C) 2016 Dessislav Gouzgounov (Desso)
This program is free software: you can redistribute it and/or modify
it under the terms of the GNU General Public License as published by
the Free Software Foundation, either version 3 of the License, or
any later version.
